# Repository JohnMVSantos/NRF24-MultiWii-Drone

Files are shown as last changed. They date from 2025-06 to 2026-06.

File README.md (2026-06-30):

# NRF24-MultiWii-Drone

This repository contains both software and electrical components for building a drone using the NRF24L01 radio modules and Arduino.

# New PCBs from PCBWay

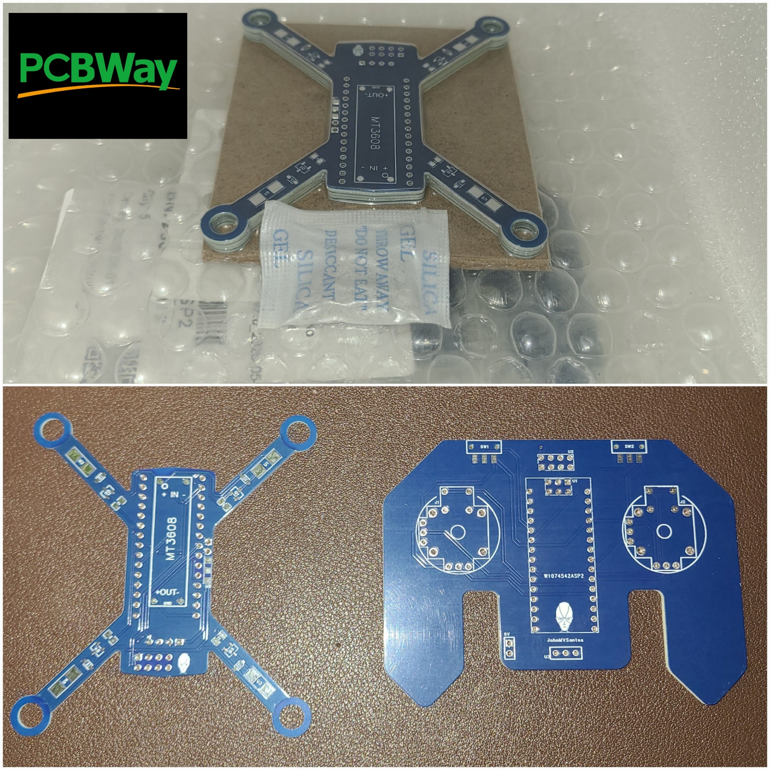
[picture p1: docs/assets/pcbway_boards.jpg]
PCBWay Boards


PCBWay provides an [excellent platform](https://www.pcbway.com/orderonline.aspx) for ordering and customizing your PCB designs. The platform provides easy-to-follow and easy-to-use PCB specifications that meets my needs such as setting the board quantity, the number of layers, the PCB thickness, material type, and much more! 

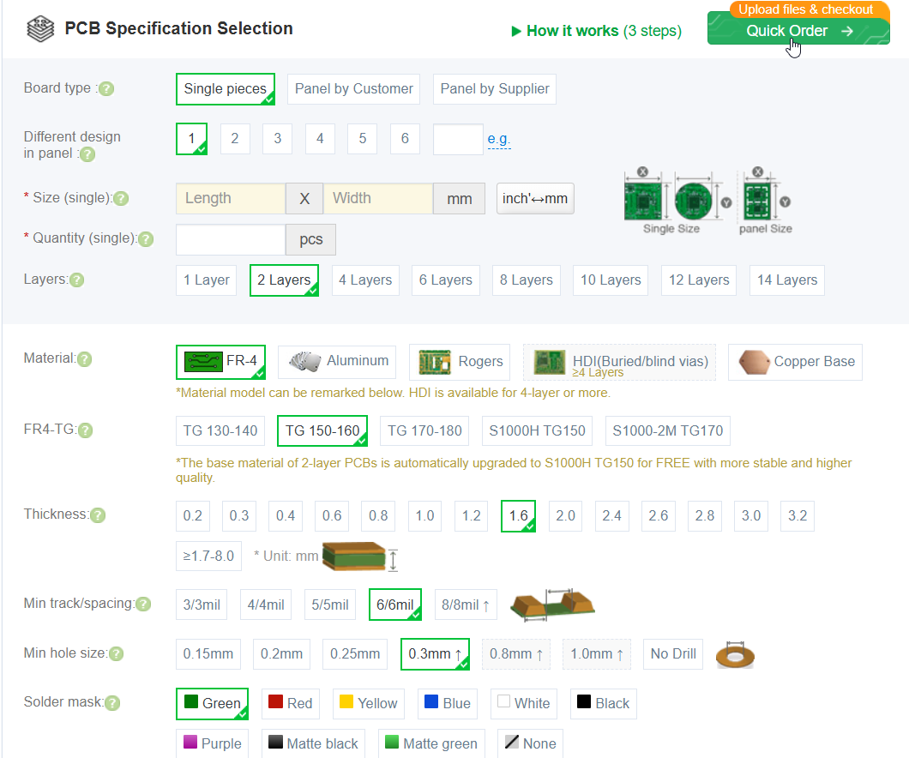
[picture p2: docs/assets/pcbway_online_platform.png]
PCBWay Online Platform


Furthermore, support is always available either through the platform or PCBWay will reach out to you directly if they require further specification or if they observe potential risks from their thorough review of your design.

Using PCBWay's online platform, I was able to import all my gerber files I designed using EasyEDA and successfully ordered the boards and arrived upon my location without any issues or concerns. This is a platform I would highly suggest for designers to use!

# Changelog

* Jun 08, 2025 [v1.0]: Prototype 1.0 [Fail] - Zero communication between controller and the drone.
* Jul 22, 2025 [v1.1]: Prototype 1.1 [Fail] - Drone short circuited with carbon fiber frame. 
* Aug 18, 2025 [v1.2]: Prototype 1.2 [Fail] - Drone keeps resetting.
* Aug 31, 2025 [v1.3]: [Prototype 1.3](https://youtu.be/l2KEjdwurtw?si=Yr7yQo37yw-8ZKtF) [Fail] - Drone does not lift off, motors out of sync. 
* Nov 30, 2025 [v1.4]: [Prototype 1.4](https://youtu.be/Q8TK0ZtKbdI?si=oR4hcLkOsZyx9zIT) [Fail] - Drone does not lift, too heavy, joystick movements does not match MultiWii simulation and drone output behaviour.
* Jan 31, 2026 [v1.5]: [Prototype 1.5](https://youtu.be/-AvNgkW_3SQ?si=GbaD0aLfVKiBPiV2) [Fail] - Drone does not lift, keeps resetting, joystick movements does not match flight pattern
* Mar 28, 2026 [v2.0]: [Prototype 2.0](https://youtu.be/SzuUDoo7Tts) [Fail] - Converted drone to a PCB, but still does not lift, one motor draws most of the power. Power to the components is not well regulated.
* Apr 27, 2026 [v2.1]: [Prototype 2.1](https://youtu.be/SVGbemywxcY) [Pass] - PCB adjustments to reduce EMF effects and better weight distributions; software adjustments for correct motor mapping.

[EasyEDA Project](https://oshwlab.com/john.santos/multiwii-arduino-drone-project)

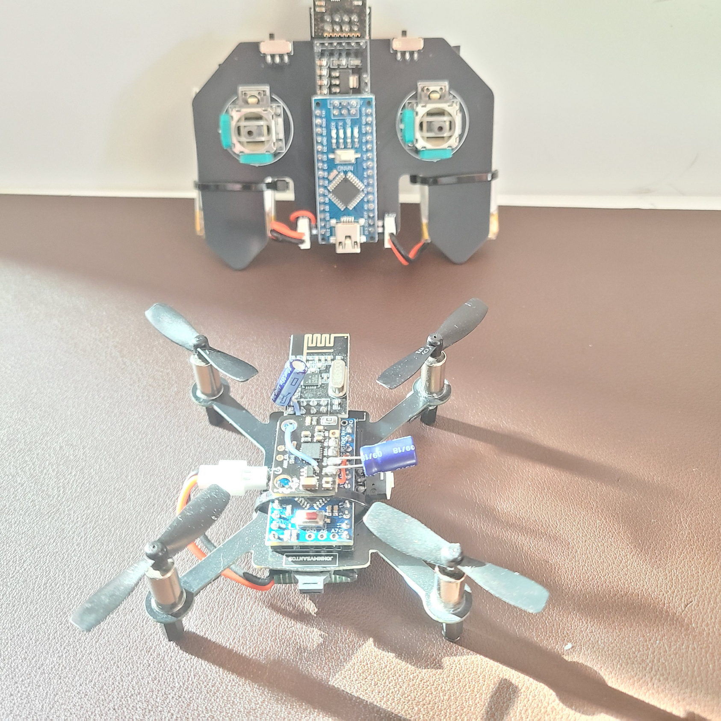
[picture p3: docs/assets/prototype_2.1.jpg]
Prototype Two


# Schematics and Diagrams

The following schematic diagram shows the wiring components and hardware for the drone.

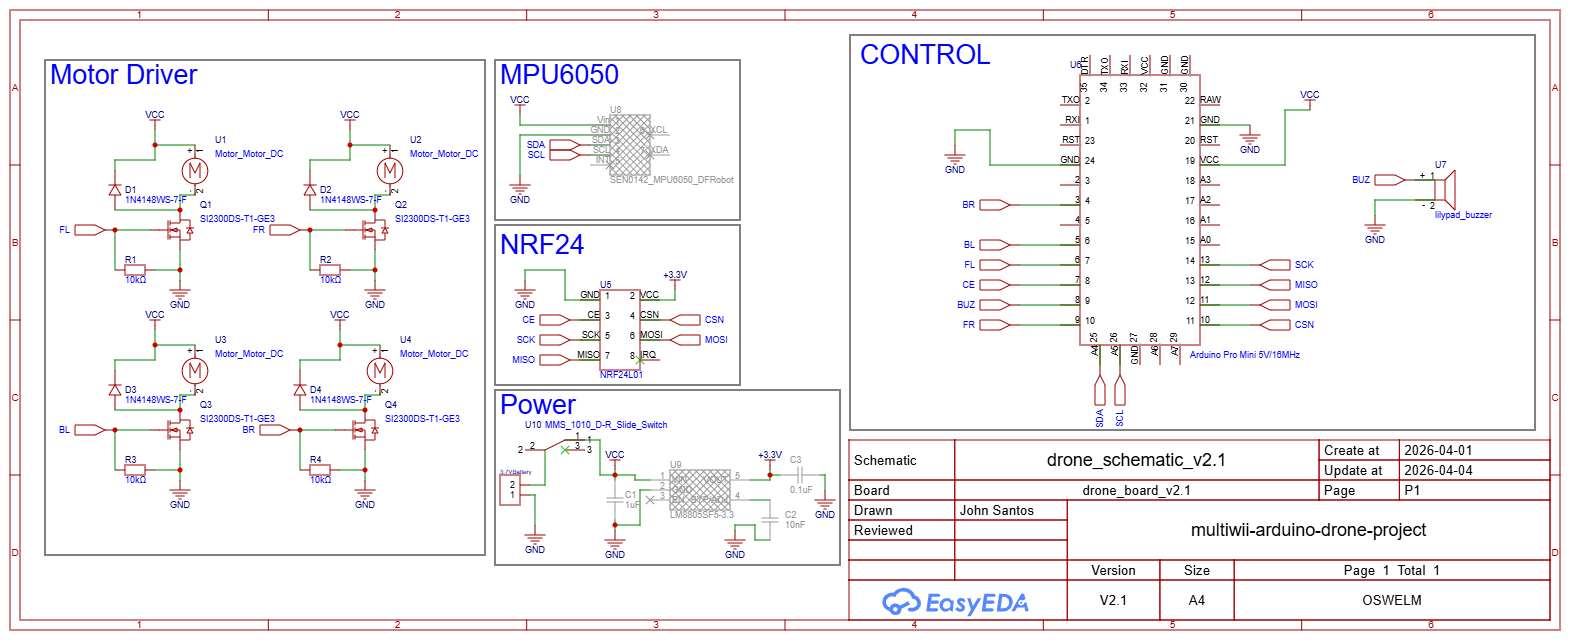
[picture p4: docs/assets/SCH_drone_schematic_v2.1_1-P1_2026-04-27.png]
Drone Schematic


| Drone PCB | Drone 3D View |
|---|---|
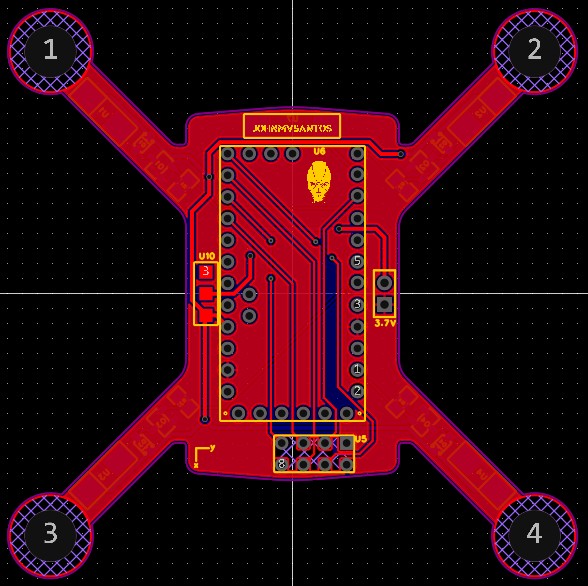
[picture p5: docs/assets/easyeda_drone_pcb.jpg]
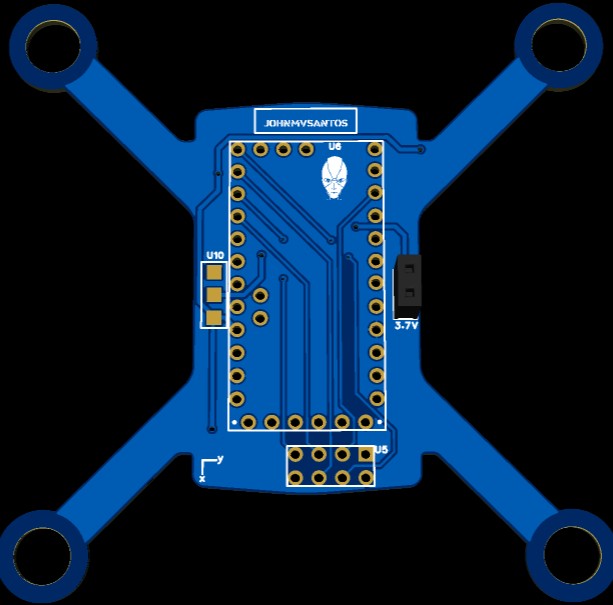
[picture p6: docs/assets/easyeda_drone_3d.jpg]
|  |  |

The following schematic diagram shows the wiring components and hardware for the drone controller. 

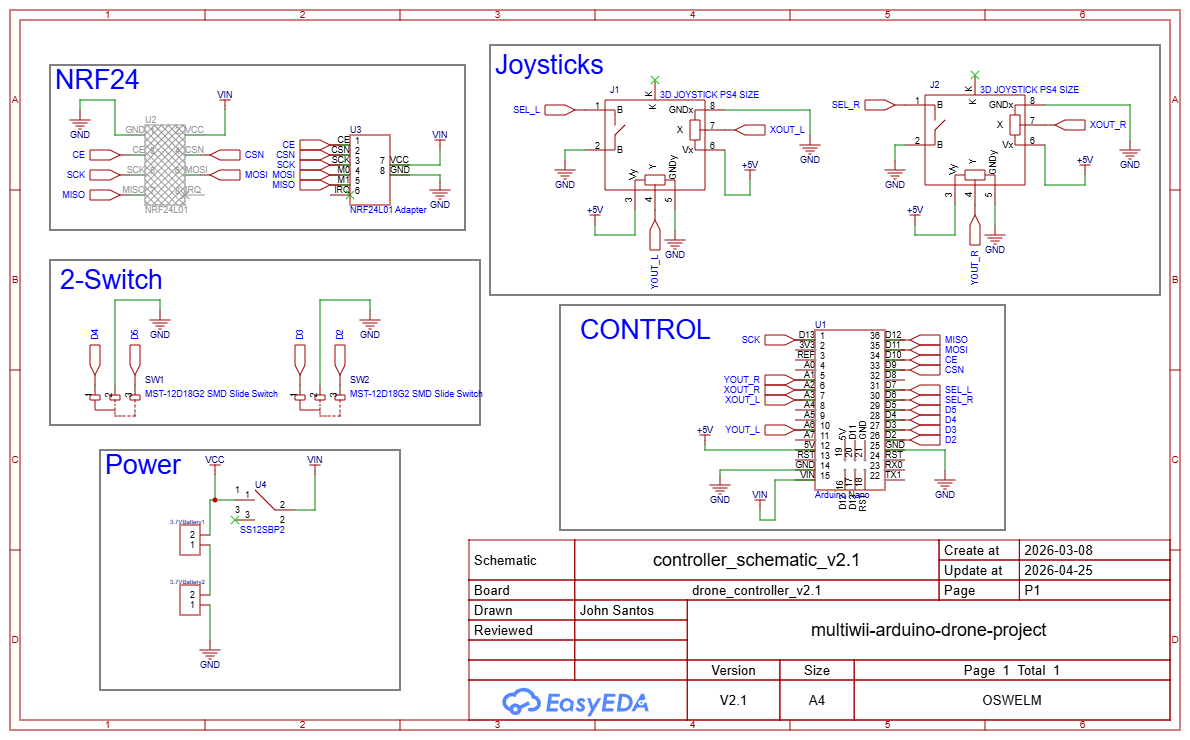
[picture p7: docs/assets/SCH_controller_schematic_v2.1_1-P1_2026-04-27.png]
Controller Schematic


| Controller PCB | Controller 3D View |
|---|---|
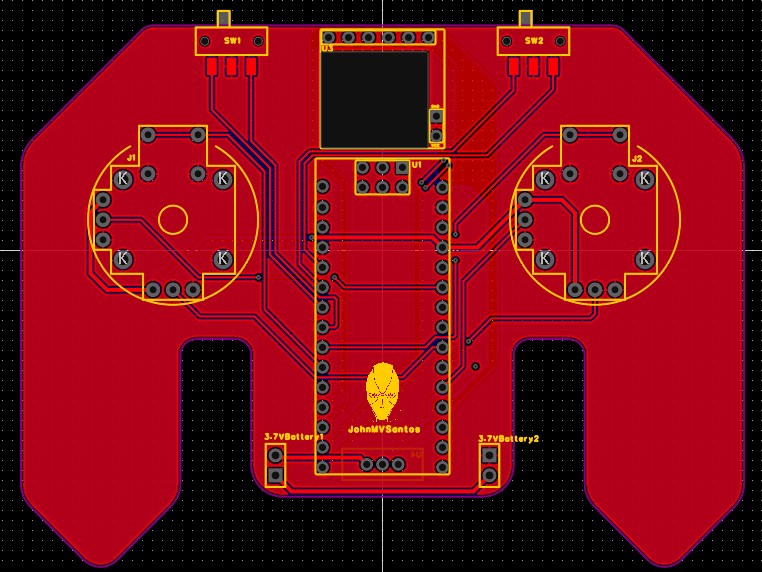
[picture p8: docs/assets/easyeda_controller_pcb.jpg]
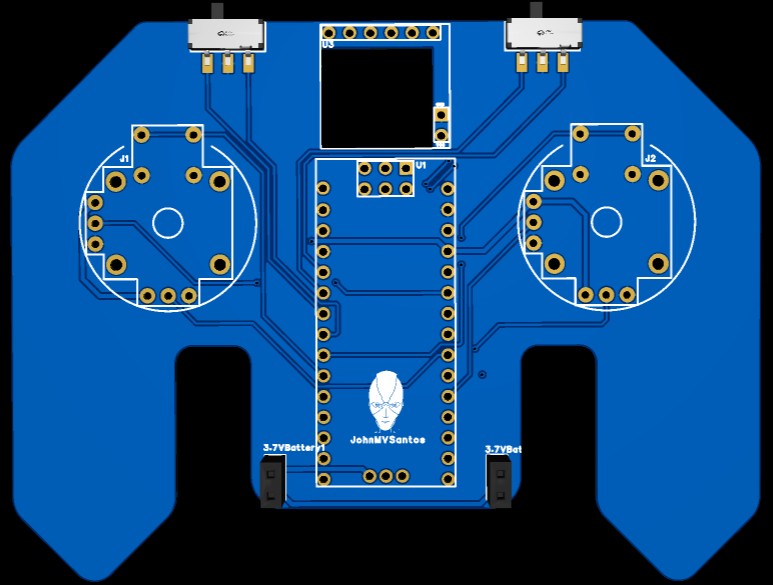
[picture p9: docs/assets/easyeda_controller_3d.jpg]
|  |  |

The following DXF sketch cutout of the drone can be found under `design_files/drone_sketch.dxf`.

| Drone Frame Sketch | Drone Frame Body |
|---|---|
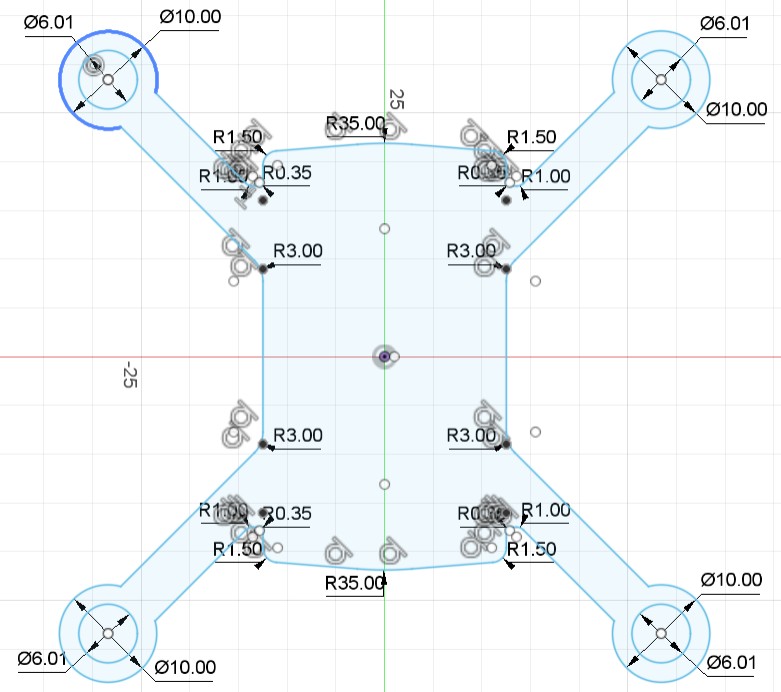
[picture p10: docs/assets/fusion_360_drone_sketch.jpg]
Drone Frame Sketch
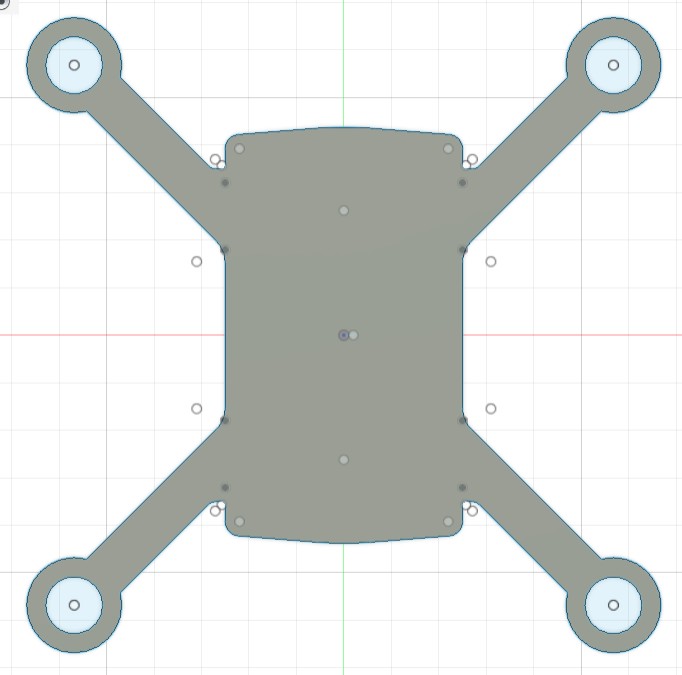
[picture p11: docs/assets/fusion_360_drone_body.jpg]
Drone Frame Body
|  |  |

The following DXF sketch cutout of the controller can be found under `design_files/controller_sketch.dxf`.

| Controller Frame Sketch | Controller Frame Body |
|---|---|
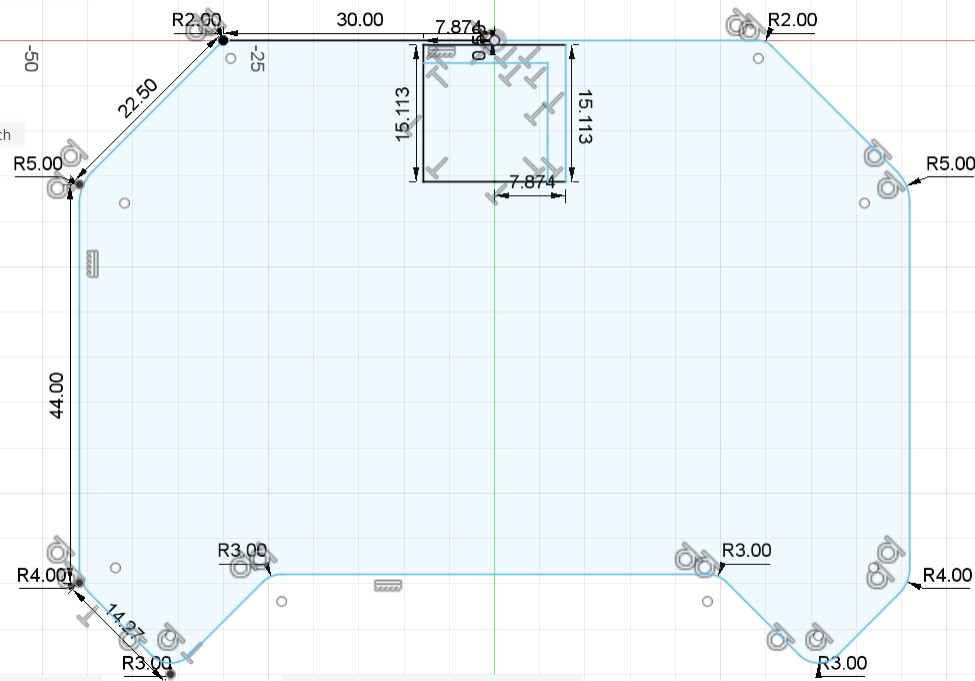
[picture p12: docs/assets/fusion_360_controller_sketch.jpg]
Controller Frame Sketch
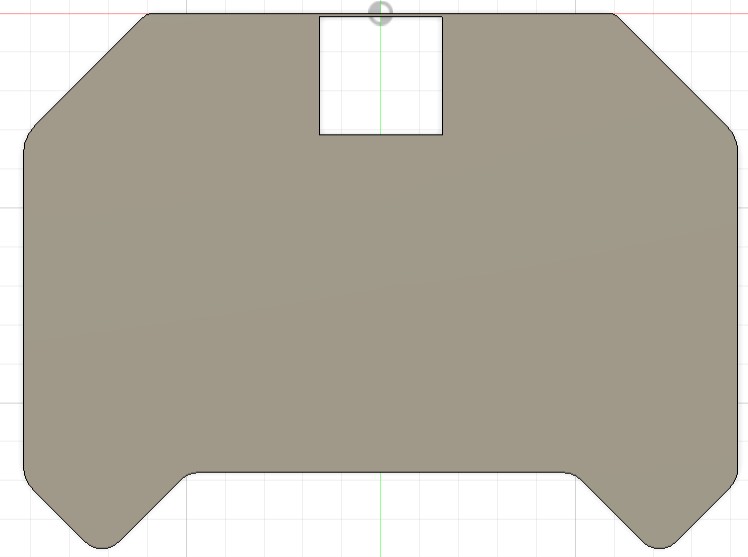
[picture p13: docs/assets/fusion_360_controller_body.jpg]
Controller Frame Body
|  | 

The tutorial for building and assembling the drone can be found under `\docs`.

# Documentation

The documentation that provides more details and tutorials on building the drone can be found under `\docs`. 

To generate the documentation using `sphinx`, follow the tutorial below with the command line. 

```shell
cd docs
```

```shell
pip install -r requirements.txt
```

```shell
make clean
make html
```

```shell
sudo apt-get install latexmk
sudo apt-get install texlive-fonts-recommended
sudo apt-get install texlive-latex-extra
```

```shell
make latexpdf
```

# Key Learnings/Takeaways

## Design Considerations:

1. Battery 25C works for this drone
2. 5V 16MHz Arduino Pro Mini is sufficient for the drone
3. Copper EMF blocking shield helps reduce the EMF noise generated by the motor driver
4. Better to place MPU6050 away from electrical noise of the Arduino and other electrical components
5. The IMU needs to be sitting flat and secured properly to prevent wobbling
6. Capacitors helps reduce power fluctuations and noise
7. Position all 4 motors evenly and in the same manner. The start rotation should be consistent
8. Smaller surface area can cause instability? I think it is better for longer arms and larger propellers to increase the drone surface area - larger lift
9. Thicker drone arms that doesn't bend is better for stability. The overall surface area of the arms and propeller should be maximized
10. Choose your components based on the design specifications. These are the components I have chosen based on the design specifications
    - 10KOhm resistor 0805 (0.125W) [CRG0805F10K](https://www.digikey.ca/en/products/detail/te-connectivity-passive-product/CRG0805F10K/2380831)
        * Ensures VGS = 0
    - Diode: [SS54FSH](https://www.digikey.ca/en/products/detail/taiwan-semiconductor-corporation/SS54FSH/18718584) (5A, 40V)
        * Maximum rated current must be greater than 2 * stall current (assuming 2-6A)
    - N- Channel Mosfet: [AO3400A](https://www.digikey.ca/en/products/detail/alpha-omega-semiconductor-inc/AO3400A/1855772) or [AO3416](https://www.digikey.ca/en/products/detail/alpha-omega-semiconductor-inc/AO3416/1855783)
        * VDS ~>20-30V is better (rated for high voltage spikes)
        * RDS ~<10mOhm is better (low power loss)
        * Gate threshold ~2.5-3.3V (turns on based on battery capacity)
        * Continuous & Pulsed Current Rating should exceed peak and continuous current draw in drone (5.5A = 25C * 0.22Ah).

1. Use an oscilloscope to check the PWM signals from the motor gates to see if it is causing sync issues with the motors - ensure consistent PWM frequency across all four motors

2. Test n-channel mosfet Integrity and ensure drain voltage approaches zero as gate voltage increases

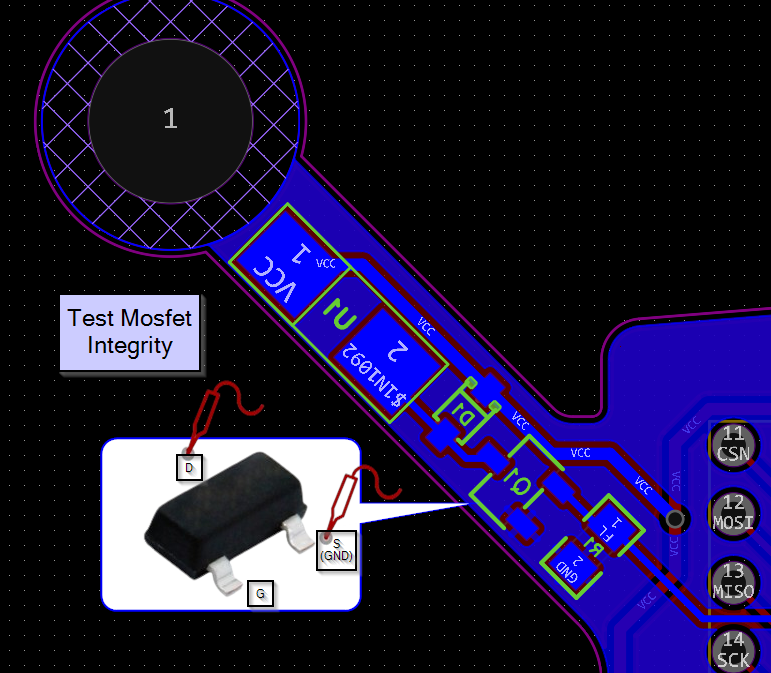
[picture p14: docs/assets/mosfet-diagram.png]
Mosfet Testing


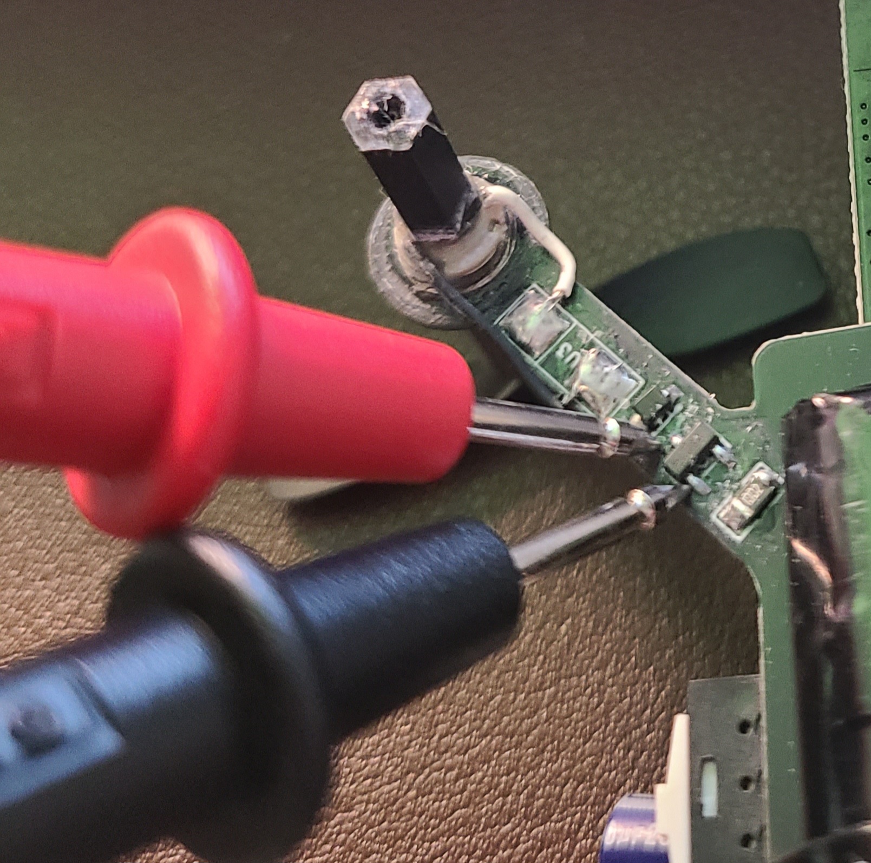
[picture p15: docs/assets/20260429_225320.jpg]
Mosfet Testing Probes


3. Test Motor terminals if voltage is received

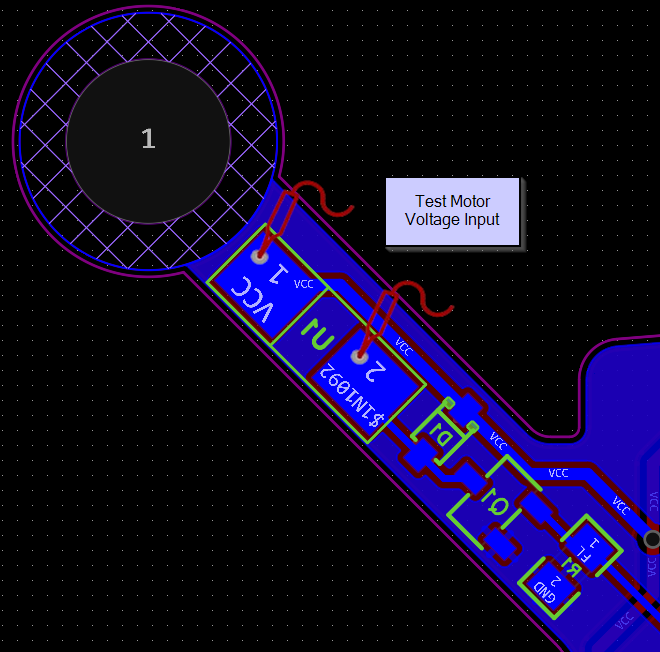
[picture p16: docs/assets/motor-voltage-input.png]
Motor Terminal Voltage


## Practical Considerations

1. Check NRF24 radio communication first before assembling the drone. Always test parts individually
2. Keep it simple and complexity should not come first. Achieve minimum functionality for initial developments
3. Better to use solder with lead, but prone to contamination (ensure proper storage)
4. Thin kapton tapes do not provide as much insulation as actual electrical tape. Though electrical tape is heavier
5. Ensure the motor power can carry the total load of the drone
6. Ensure prototype works before designing a final PCB

# Successful Vendors

These are the lift of successful vendors that sold the components needed for this project that worked. 

- **Robojax**: Arduino Pro Mini 5V 16MHz 
- **HiLetGo**: NRF24L01+PA+LNA Transeiver Module
- **Aideepen**: NRF24L01 Transeiver Standard Module
- **Aideepen**: Arduino Nano Board
- **Fytoo**: 3.7V 600mAH LiON batteries - used for the controller
- **Fytoo**: 3.7V 220mAH LiON 25C battery
- **WWZMDiB**: Mini USB to TTL Serial Converter Adapter, 3.3V/5.5 V FTDI Breakout Board for Arduino
- **Wishiot**: Thumb Joystick Module Dual Axis Sensor for Arduino
- **DFRobot**: MPU6050 Gyro + Accelerometer Module
- **Digikey**: Surface mount components (resistors, diodes, n-channel MOSFETs, capacitors, etc)
- **Midzooparts**: Lilypad Buzzer Small Speaker Module for Arduino
- **Crazepony**: 4pcs 6x15mm Motor (Speed: Insane) 19000KV, 70000 RPM@3.7V

These are the list of vendors that sold components that did not work or were faulty for this project.

- **Hutomwua**: Arduino Pro Mini 5V 16MHz (Did not meet specifications or seems to be 10MHz on the backside - not advertised)
- **ELEGOO**: Arduno Nano (Faulty and did not program)
- **Fytoo**: 3.7V 1000mAH LiON batteries (potentially drew too much current and burned the board?)
- **Aideepen**: NRF24L01+PA+LNA Transeiver Module (Faulty and did not communicate)

# Future Work

## v3.0
- If it doesn't fly (use Arduino Nano board and standard MPU6050? This requires regulators since Arduino Nano inputs 5V)
- Incorporatte FPV camera - make it see
- Add AI detections and features

## v4.0
- Custom FPV GUI with IMU readings (Can a single transmitter have two recievers (Controller + GUI)? )

# Credits

Original drone software is credited to [iforce2d](https://www.youtube.com/@iforce2d).

## Drone Tutorial - Max Imagination

Watch the video (https://www.youtube.com/watch?v=Sa6EslOHsI0)

* [Elektor Labs blog post](https://www.elektormagazine.com/labs/make-a-tiny-arduino-drone-with-fpv-camera)
* [Project Files](https://drive.google.com/drive/folders/1mWTCPN2daOcmTa4wUF0j8qPXhXvxLfkK)

## Drone Tutorial - ElectroNoobs

Watch the video (https://www.youtube.com/watch?v=J0x4ChjUS00&t=719s)

# Support Forums

* https://www.instructables.com/Make-a-Tiny-Arduino-Drone-With-FPV-Camera/
* https://www.elektormagazine.com/labs/make-a-tiny-arduino-drone-with-fpv-camera

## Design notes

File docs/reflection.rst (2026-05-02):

.. _reflection:

Reflection
===========

Log Entry: June 8, 2025
------------------------

The inspiration behind this project stems from `Max Imaginations' Mini FPV Drone Tutorial <https://www.youtube.com/watch?v=Sa6EslOHsI0>`_. 
Watching that video sparked the idea to create a similar design with my own custom modifications to better understand the process of engineering design.
Having recently graduated with a bachelor's degree in electrical engineering, I wanted to build more experiences in the field of electrical engineering. 
I found that by embarking on this project, I could apply my knowledge I gained in my studies to a practical application and also explore new concepts and ideas along the way.

It was not easy to commit to the project in the beginning because deep down I knew that I would be spending a lot of time and resources on this project even more so that this project
requires a lot of electrical and mechanical components that could be quite expensive. Furthermore, I am also working full-time as a software engineer and finding 
free time to work on this project was a challenge. Alot of the time spent on this project was during the weekends and late nights after work which required a lot of sacrifice. 

However, I was determined to see this project through; to better myself as an electrical engineer and to create something new and challenging despite my lack of 
personal experiences in building drones or electrical engineering projects in general. 

The start of the project was slow as I had to first list all the electrical and mechanical components I needed to build the drone and its controller. I wanted to 
gather as much detail as possible such as the cost, size, and weight of each component to assess its viability. Most of the components I had used 
remains the same as Max Imaginations' Drone, but I wanted my own custom design of the frame.

After listing the components for the drone and the controller, I had started to replicate the wooden frame design by Max Imagination, but after recreating the frame,
I found that it was too small and simple looking for my liking. I wanted a more streamlined and modern design so I explored other designs online that uses carbon fiber. 
I eventually sketched out a design that I liked and drew a blueprint of the components for my frame as a cutout template. I then moved on to purchasing a 0.5mm thick carbon fiber sheet.
I printed the cutout template and made the cutouts on the carbon fiber sheet for each component of the frame using a dremel tool. The frame was eventually built
using carbon fiber and M2 screws and nuts to hold the components in place.

The next step was building the electrical components of the drone. I had to first study the circuit provided by Max Imaginations' Drone and I also redrew the circuit in EasyEDA for my own references.
After drawing the circuit schematics for the drone and the controller, I then purchased the components from Amazon, Digikey, and Mouser. This stage was also a bit slow as I had to 
wait for the components to arrive before I could continue with the project. There were a lot of delays due to some parcels being lost and I had to reorder these lost components from different sources. 

Once all the electrical components arrived, I started building the circuit for the drone by soldering the components together. I had little experiences with soldering
electrical components so I had some challenges in this area. Primarily, the soldering iron oxidized quickly which is probably due to poor techniques I am employing or poor
solder material that I am using. I had to switch solder tips quite frequently, but this wasn't very efficient as I ran out of solder tips and I was forced
to use an ineffective soldering iron which led to poor soldering quality. This stage started to take a bad turn for me as the poor soldering quality 
affected the overall quality of the design as the circuit was prone to short-circuiting and the components not working as expected.

I reached a stage where I had the circuit for the drone built and assembled and programmed using Arduino, but there were lots of failures in MultiSim. The drone was able to 
be programmed, but it did not interface well with MultiSim as the MPU6050 Gyro movements was not translated in the simulation and only appeared as a bunch of noisy signals. Furthermore,
the MPU only seemed to move digitally when grounding pin D12 on the Arduino Pro Mini which was not expected. At this stage I was not satisfied with the current work on my drone as I am starting to
see failures and weaknesses in my design. So I had to take a step back and reflect on my design and make revisions to resolve the issues I was facing. I've documented
the issues with this design which I have indicated as "Prototype 1" under the :ref:`Prototypes section <prototypes>`.

In this stage, I have planned to recreate the design and name it as "Prototype 1.1" with the fixes needed for the issues from the current design.

Log Entry: July 22, 2025
-------------------------

This log will provide details to the outcome of Prototype 1.1 and the revisions made to the design. This prototype had a much more compact design 
with shorter connections and lighter wires. Furthermore, the controller had a proper enclosure recycled from a toy controller enclosure with modifications
to fit the new components. However, this prototype also failed the final testing. The initial work for this prototype started by assembling the electrical components by resoldering the drone circuit using 28 AWG silicon copper wires. 
After the drone circuit is complete, the next task was to modify an old toy controller enclosure to fit the new controller components. This task involved drilling and cutting
certain parts of the enclosure using a dremel tool. Once the enclosure was fitted, the new components were installed and soldered. 

In this stage, the drone circuit and the controller circuit are both assembled and programmed for testing. The first test on the drone had some success
in which the IMU was able to ready the gyro movements. However, the flight controls in MultiSim were still unresponsive to the joystick movements from the controller. I found later
on that the radio modules from the controller were faulty. This test involved setting up a simple communication between two of the spare radio modules
on a breadboard. After reordering a new set of radio modules, I was able to get clear communication between these new modules. Moving forward, the drone
was also able to capture the signals sent from the controller's joystick movements as shown in MultiSim. Lastly, I was not fully confident that the drone enclosure was properly insulated,
so I tested the drone responding without it's enclosure. This testing was successful as the motors properly relayed the controller's signals with the expected
motor speed based on the throttle joystick movements. However, the drone failed once I tested with the drone enclosure attached. I suspect, I had short circuited the electrical components of the drone
because of its carbon fiber frame. I had regretted not testing the insulation of the frame even with Kapton tape. Again at this point, I needed to take a step back again
and assess the failures of this prototype and make more revisions to resolve these issues. More details of this assessment are provided under the :ref:`Prototypes section <prototypes>`.

In this stage I have ordered replacements for the damaged components such as the Arduino Nano, Arduino Pro Mini, NRF24L01 radio modules, and the controller battery.
I have planned to recreate the design and name it as "Prototype 1.2" with the fixes needed for the issues in the current design.

Log Entry: August 18, 2025
---------------------------

This log will provide details to the outcome of Prototype 1.2 and the revisions needed to be made for the design. After implementing this prototype, the behaviour of the drone
was quite erratic. The drone kept resetting when throttle is decreased near zero. It seems to keep resetting and attempts to recalibrate the IMU. The motor responses were rare and seldom spins. When the motor does respond, it 
responds in bursts and then the drone resets. Looking at the MultiSim outputs, the AUX1 and AUX2 were correctly translated including the joystick movements for roll, pitch, yaw, and throttle levels. So I don't think the issue
has to do with the controller, rather with the drone itself. 

I suspect possible issues with the drone circuit listed below.

1. The battery discharge rate is too low (25C) and that a proper drone battery with a higher discharge rate (30C or higher) is needed
2. The power for the radio is not consistent and requires a 10uF filtering capacitor at the NRF24 power inputs
3. The power for the Arduino Pro Mini is not consistent and requires a 100uF filtering capacitor
4. The power lines has a large AWG (small thickness) where the current cannot be supplied properly
5. Motor PWM signals could be too weak to drive the motors
6. Potential EMF noise or leaks is affecting the IMU readings? 
7. The Arduino Pro Mini is faulty which was purchased from "Hutomwua". The previous prototypes was working which was purchased from "Robojax"

Looking for a battery replacement greater than 25C was quite a challenge as most of the batteries I found were 25C or lower. It was recommended to use "Turnigy Nano-Tech" batteries for their high performance,
but these were always not available and kept being out of stock due to their high demand. Although I did manage to find a 30C LiPO battery, not from Turnigy, but from AMZZN, it still didn't
resolve the main issue. The drone behaved a bit better, but most of the resetting issue persisted. 

I moved forward by adding filtering capacitors at the radio module and Arduino Pro Mini power inputs, but this did not resolve the issue. I also ensured the solder for the power connections and the 
radio connections were solid and well connected, but this also did not resolve the issue. I even created a new motor driver with new MOSFETs and diodes as I had assumed this circuit also short circuited from the previous prototype, but this still this replacement did not resolve the issue. 

I then suspected, it has to do with the software and that the PWM signals were too weak to drive the motors. Unfortunately, I do not have an oscilloscope to verify the weake PWM signals, but I found the factor in the MultiWii software
that tunes the PWM outputs. Following the tutorial by Max Imaginations, the variable should be `float adjustmentFactor = 0.255` in line 1069 of output.cpp. I set this value to 0.255 from the default of 1, but this did not resolve the issue. However, it did tune the buzzer noises lower.
As a future work, it seems that it will be best to purchase an oscilloscope to confirm this suspicion. 

Moving forward, I retraced my steps and assessed the instructions for properly arming the drone using MultiSim. First the AUX1 and AUX2 should be set high for arming the drone and the beeper respectively. Once set, the drone accelerometer should
be calibrated and then read and write to save the changes. To arm and calibrate the drone, the AUX1 should be set low and the throttle and pitch controls are set to zero until the calibration noises are in effect. Once in effect, wait atleast 3 seconds
to apply the calibrations. With these steps, the drone still didn't manage to respond. 

My next suspicion is the hardware itself. I purchased the Arduino Pro Mini from "Hutomwua" which did not work, I intend to purchase the Arduino Pro Mini from "Robojax" which worked in the previous prototype (v1.1) where the motors actually responded. 
I have purchased the same Arduino Pro Mini and will try again in the next version. Furthermore, I will confirm the specifications for the MOSFETs, diodes, and resistors are properly rated for the circuit and the power requirements. More details of this assessment under the :ref:`Prototypes section <prototypes>`.
I have planned to recreate the design and name it as “Prototype 1.3” with the fixes needed for the current design.

Log Entry: August 31, 2025
---------------------------

This log will describe the details to the outcome of Prototype 1.3 and the revisions made to the design. Based on the last suspicion that the hardware purchase for the Arduino Pro Mini
was the source of the issue. This suspicion turned out to be true. Looking at the Arduino Pro Mini purchased from "Hutomwua", the board frequency was only 10MHz (from the backside). This did not meet specifications 
for a 5V 16MHz board. I repurchased the Arduino Pro Mini from "Robojax" which was 5V 16MHz and this resolved the issue. The drone was able to respond to the controller's joystick movements.

However, the design is still not perfect as further issues continued. Although the motors responds to the joystick movements, the drone behaves erratically unable to make a proper liftoff.

The possible issues are listed below.

1. The drone is not calibrated properly
    - The drone needs to sit on a flat surface for a proper calibration
    - The accelerometer and the gyroscope needs proper calibration
    - Adjust settings in MultiWii configuration with max smoothness
2. Motor direction is wrong
    - This can be verified by feeling if the air is being pushed upwards
    - Record slow motion video to see the direction of the motors
3. The motor RPMs are not the same and unsynchronized
4. The forward direction of the MPU6050 is in the opposite direction
    - Rewire orientation of the motors to have face the MPU6050 in its forward direction
5. The drone is still too heavy and certain weights of the components are not balanced causing the center of gravity to be offset
    - Remove heavy motor mounts and just rely on superglue to attach the motors
6. The arms of the drone are limble which causes wobbling during flight
    - Reinforce the arms with a stronger material that doesn't bend such as popsicle sticks

More details of this assessment under the :ref:`Prototypes section <prototypes>`. I have planned to recreate the design and name it as “Prototype 1.4” with the fixes needed for the current design.

Log Entry: November 30, 2025
-----------------------------

This log will describe the details to the outcome of Prototype 1.4 and the revisions made to the design. In this prototype, the drone accelerometer was calibrated 
and an EMF copper blocking shield was installed to prevent interference from the motor controller to the Arduino Pro Mini. Furthermore, the motor direction was verified
where the top left motor spins clockwise, top right motor spins counter-clockwise, bottom left motor spins counter-clockwise, and the bottom right motor spins clockwise. 
The bottom right propeller was wrong preventing the air from being pushed downward. Furthermore for stability reasons, the arms were replaced with popsicle sticks
to prevent any bending or oscillations, the motors were also superglued to the arms. 

Although the design is still not perfect as further issues continued. The possible issues are listed below.

1. IMU wobbles, unsecure mount
2. Frame is yet still too heavy
3. Smaller propellers + arm surface area - more unstable
4. Battery is mounted at the bottom which makes it hard to connect
5. Wrong drone output behaviour from the joystick movements - needs software correction
6. Needs PID tuning for the roll, pitch, and yaw

New Frame Requires:
- Lighter, thinner frame
- Thick arms with more propeller surface area
- Battery mounted on top for easier connection and center of gravity adjustment
- Superglued motors and soldered connections
- Reduce weight as much as possible

The current configurations with the expected behaviour and the actual behaviour are noted below

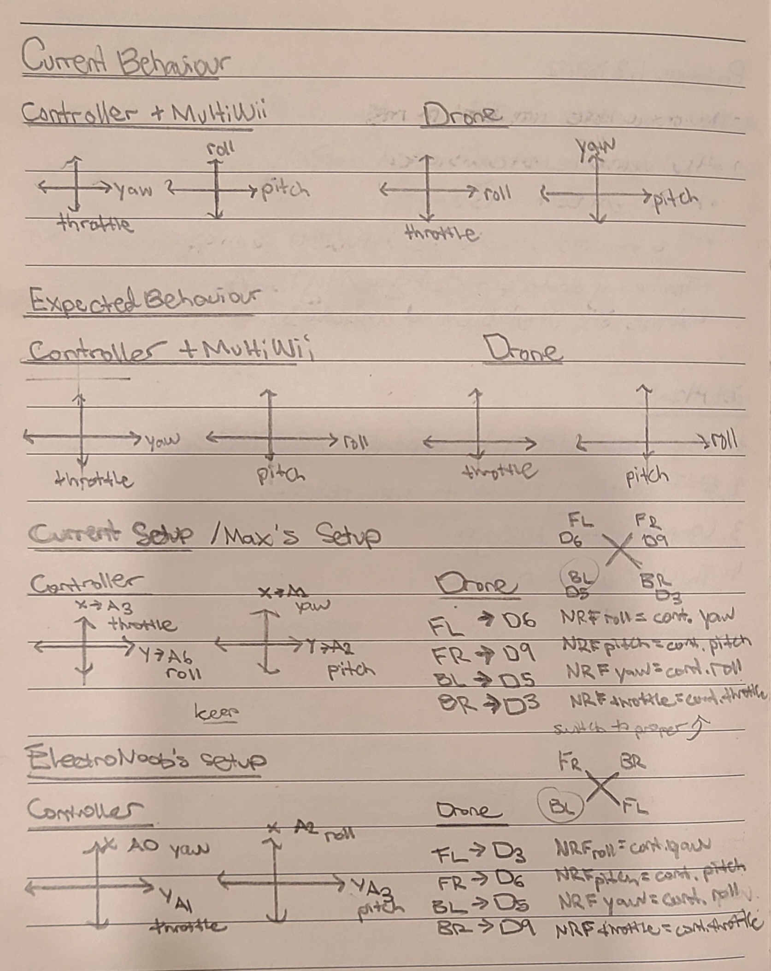
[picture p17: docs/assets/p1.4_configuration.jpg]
Prototype 1.4 Configuration


More details of this assessment under the :ref:`Prototypes section <prototypes>`. I have planned to recreate the design and name it as “Prototype 1.5” with the fixes needed for the current design.

Log Entry: January 31, 2026
----------------------------

This log will describe the details to the outcome of Prototype 1.5 and the revisions made to the design. 
This prototype is based on redesigning the frame to use popsicle sticks and superglue to reduce the overall weight of the drone and to secure the components in place.
However, this prototype is still unable to lift off, and suspecting it could be due to weight imbalance of the components, the motors spin at different RPMs and unsynchronized, or the motors spin in the wrong direction as I felt the air being pushed upwards with my hand. 

The next prototype will explore designing a custom PCB for the drone to reduce the wiring connections and to have a more compact design. Furthermore, I will also explore different motor driver components to withstand potential current or 
power rating issues. More details of this assessment under the :ref:`Prototypes section <prototypes>`. I have planned to recreate the design and name it as “Prototype 2.0” with the fixes needed for the current design.

The possible reasons for the resetting issue are listed below.
1. The Arduino Pro Mini is not receiving enought power (needs 5V, but getting only 3.3-4V)
2. Power should be directly to raw pin instead of VCC pin, or both?
3. Update MultiWii settings exactly to Max Imagination's settings
4. Resistor at the reset pin to avoid constant drone resetting? (Resetting is primarily due to EMF effects or loss of power from the battery)
5. Missing EMF blocking copper sheet under the IMU (cover with clear tape and add ground wire)
6. EMF Copper Blocking Shield under the Arduino Pro Mini- [Helped with wobbling]
7. Software issue? Try disabling FORCE_GYRO settings in the software

Experimented with possible solutions to out of sync motors.
1. Issue with propeller - Wrong propeller used on back left [Helped with stability]
2. Motor direction is correct (top left is CW, top right is CCW, bottom left is CCW, bottom right is CW)
3. Solder motor wirings directly - [Helped with loss of power to the motors]
4. Switch forward/backward motor wirings + Max's MultiWii settings. [Was not quite useful]
5. Research imbalance, seems that left side of the drone pulls up more:

	- incorrect flight controller orientation
	- wrong motor/propeller configuration
	- or a damaged component like a motor or ESC

A list of unknowns I encountered.
1. On multiwii the IMU yaw just rotates even though the drone is placed flat on the table.
2. Calibrate controller settings to match joystick?
3. Max Imagination's right joystick is rotated - should also rotate

Log Entry: March 28, 2026
----------------------------

This log will describe the details to the outcome of Prototype 2.0 and the revisions made to the design. In this prototype, a PCB was designed in EasyEDA and manufactured in JLCPCB.
The motivations behind this design is to stablize the wiring connections and to have a more compact design.  Furthermore, I have also chosen chosen different motor driver components
to withstand potential current or power rating issues. These are the final components I have chosen for this prototype.

- 10KOhm resistor 0805 (0.125W) [CRG0805F10K](https://www.digikey.ca/en/products/detail/te-connectivity-passive-product/CRG0805F10K/2380831)
        * Ensures VGS = 0
- Diode: [SS54FSH](https://www.digikey.ca/en/products/detail/taiwan-semiconductor-corporation/SS54FSH/18718584) (5A, 40V)
    * Maximum rated current must be greater than 2 * stall current (assuming 2-6A)
- N- Channel Mosfet: [AO3400A](https://www.digikey.ca/en/products/detail/alpha-omega-semiconductor-inc/AO3400A/1855772) or [AO3416](https://www.digikey.ca/en/products/detail/alpha-omega-semiconductor-inc/AO3416/1855783)
    * VDS ~>20-30V is better (rated for high voltage spikes)
    * RDS ~<10mOhm is better (low power loss)
    * Gate threshold ~2.5-3.3V (turns on based on battery capacity)
    * Continuous & Pulsed Current Rating should exceed peak and continuous current draw in drone (5.5A = 25C * 0.22Ah)

However, despite the changes to the design, this drone is still unable to fly and behaves more poorly. When testing the assembled PCB, it looks like most of the current
is being drawn towards the back right motor causing it the only motor to spin. When I disconnect this motor, the other three motors spin, but the resetting issue persists. 
It looks like separating the motor driver across the arms does not mitigate the EMF effects causing the drone to keep resetting. I also tried adding a 100uF capacitor between the power
and ground pin of the MPU6050, but this does not resolve the reset issue. 

These are the list of issues for this prototype.

- Bottom right motor keeps spinning uncontrollably and the only single motor that spins when all motors are connected (need to find a way to separate power between the motors and the microcontroller)
- Better larger battery did not help
- 100uF at the MPU6050 did not help
- Thicker power lines by reinforcing the connections with external wires did not help 
- Drone still keeps resetting
- MultiWii is an old software and no longer used - may not even be properly installed due to requiring a specific Java version. 

The possible reasons for these issues are listed below.

1. Power management issues - the battery is not strong enough to drive both the Arduino Pro Mini and the Motors
2. Power lines are too thin
3. All lines in this PCB are set to 0.254mm which is the default in EasyEDA. Also the power lengths to the motors should be similar
4. 90 degree line traces are evident in these connections which can cause impedence issues

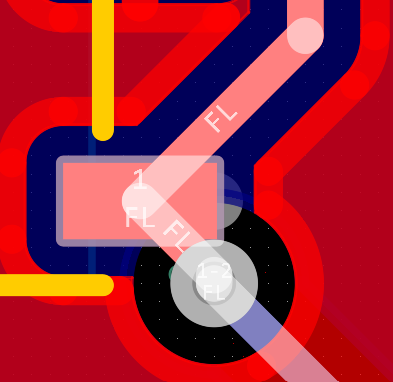
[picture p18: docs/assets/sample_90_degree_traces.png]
90 Degree Line Traces


5. Absence of grounded EMF copper blocking shield - a bit hesitant with this since I have tried it before and it did not resolve the resetting issue
6. Props are placed wrong (air is pushed upward)
7. Motor placement are not consistent - wiring needs to be at the same start rotation
8. Use the exact same components as Max's design such as 1N4148
9. Need to use better power switch (SPST) - might not be driving enough current to the motors
10. Would adding filtering capacitors at the motors help?
11. Check PWM signals from motor gates see if it is causing sync issues with the motors
12. Test controller linear increase in throttle to see if all motors respond consistently
13. Test individual motors at full power with scale load?

Log Entry: April 26, 2026
---------------------------

This log will describe the details to the outcome of Prototype 2.1 and the revisions made to the design. 
The PCB design involves placing the motor driver at the bottom layer along the arms of the drone. 
This was an excellent design choice since the drone was more stable and the resetting issue was less frequent which could indicate the EMF effects towards the microcontroller was reduced. 
Furthermore, I have tried to balance the weight by distributing the components more evenly on the PCB. For example, the ON/OFF switch and the power pins are placed in opposite ends of the drone; the NRF24L01 is more centered and finally the battery is secured at the bottom centered on the PCB.
I have also used a better battery with a higher discharge rate of 30C, 450mAH, and 3.7V for better power supply to the drone. 
I have also updated the power lines to be 0.45-0.50mm thick in comparison to traditional lines only at 0.254mm thick. This reduces resistance added on the power lines for more direct current flow. There are also no 90 degree traces in the PCB design which can cause impedance issues. 
These power lines also have similar lengths to ensure the power is distributed evenly across the motors.
I have also reverted to using 1N4148 diodes and S12300DS n-Mosfets for the motor driver as these are commonly used in drone motor drivers and should be sufficient for the power requirements of the drone. Although I have noticed that one of the mosfets burned out and had to replace this - this occurence was uncommon.
It was necessary for me to add 10uF capacitors at the power inputs of the NRF24L01. Otherwise, the signal becomes lost and the drone throttle continuously increases until it reaches the maximum state; throttle down is no longer responding. This issue caused two of the motors (FL and BL) to burn out. After adding this capacitor, the signal is more stable and the drone responds properly to the controller's commands.
Though the front left motor is unstable - sometimes doesn't spin (no issues in the  mosfets or diodes in the driver) - poor motor/connection is plausible.
In addition, I have also added 100uF capacitor at the power input of the MPU6050 to stabilize any remaining reset issues. After adding this capacitor, I no longer found any occurences of the drone resetting.
The motor placements are also more consistent and the wiring is at the same start rotation. The propeller placements are also correct as the air is being pushed downwards.
Next I have checked the frequency of the PWM signals at full power to ensure it is consistent across all motors. Using an oscilloscope, I found that each PWM pins outputs a consistent 5.0MHz which is enough to drive the motors.
In the MultiWii software, I have simulated alot of movements in the drone to ensure the IMU correctly translates the drone movements.

The biggest change was remapping the motor designations in the software output.cpp based on the following comparisons to various projects and pin designations.

.. list-table:: Motor Pin Configuration Comparison
   :header-rows: 1
   :widths: 15 20 25 18 10 15

   * - Motor
     - Intended Orientation
     - Max Imagination (Current Setup)
     - Electronoobs
     - Code
     - Test Results
   * - Motor[0]
     - BR
     - D3
     - D9
     - D9
     - FR
   * - Motor[1]
     - FR
     - D9
     - D6
     - D6
     - FL
   * - Motor[2]
     - BL
     - D5
     - D5
     - D5
     - BL
   * - Motor[3]
     - FL
     - D6
     - D3
     - D3
     - BR

It seems that the code matches Electronoobs setup. Since I have followed Max Imaginations PWM wirings, I have to modify the software to reflect this wiring. 

Thus the software needs to match the following configuration.

* Motor[0] => FR
* Motor[1] => FL
* Motor[2] => BL
* Motor[3] => BR

So the following lines in output.cpp was modified to:

**Before**

.. code-block:: shell

    motor[0] = PIDMIX(-1,+1,-1); //REAR_R
    motor[1] = PIDMIX(-1,-1,+1); //FRONT_R
    motor[2] = PIDMIX(+1,+1,+1); //REAR_L
    motor[3] = PIDMIX(+1,-1,-1); //FRONT_L

**After**

.. code-block:: shell

    motor[0] = PIDMIX(-1,-1,+1); //FRONT_R
    motor[1] = PIDMIX(+1,-1,-1); //FRONT_L
    motor[2] = PIDMIX(+1,+1,+1); //REAR_L
    motor[3] = PIDMIX(-1,+1,-1); //REAR_R

Regarding the controller, I have also designed a PCB version of the controller. However, the inital protoype is still better at maintaing the communication with the drone. I still need to take a closer look into why the connection quickly gets lost with this new controller, despite the same connections.
I will try adding a filtering capacitor at the power input of the NRF24L01 to stabilize the signal and reduce noise. Otherwise, I will take a look at reusing the same NRF24L01 that works from the previous controller prototype.

Key Learnings/Takeaways
-----------------------

Design Considerations:

1. Battery should be 25C and higher
2. 5V 16MHz Arduino Pro Mini is sufficient for the drone
3. Copper EMF blocking shield helps reduce the EMF noise generated by the motor driver
4. Better to place MPU6050 away from electrical noise of the Arduino and other electrical components
5. The IMU needs to be sitting flat and secured properly to prevent wobbling
6. Capacitors helps reduce power fluctuations and noise
7. Position all 4 motors evenly and in the same manner. The start rotation should be consistent
8. Smaller surface area can cause instability? I think it is better for longer arms and larger propellers to increase the drone surface area -larger lift
9. Thicker drone arms that doesn't bend is better for stability. The overall surface area of the arms and propeller should be maximized
10. Choose your components based on the design specifications. These are the components I have chosen based on the design specifications

- 10KOhm resistor 0805 (0.125W)   `CRG0805F10K <https://www.digikey.ca/en/products/detail/te-connectivity-passive-product/CRG0805F10K/2380831>`_
    * Ensures VGS = 0
- Diode: `SS54FSH <https://www.digikey.ca/en/products/detail/taiwan-semiconductor-corporation/SS54FSH/18718584>`_ (5A, 40V)
    * Maximum rated current must be greater than 2 * stall current (assuming 2-6A)
- N- Channel Mosfet: `AO3400A <https://www.digikey.ca/en/products/detail/alpha-omega-semiconductor-inc/AO3400A/1855772>`_ or `AO3416 <https://www.digikey.ca/en/products/detail/alpha-omega-semiconductor-inc/AO3416/1855783>`_
    * VDS ~>20-30V is better (rated for high voltage spikes)
    * RDS ~<10mOhm is better (low power loss)
    * Gate threshold ~2.5-3.3V (turns on based on battery capacity)
    * Continuous & Pulsed Current Rating should exceed peak and continuous current draw in drone (5.5A = 25C * 0.22Ah)

Testing Considerations:

1. Use an oscilloscope to check the PWM signals from the motor gates to see if it is causing sync issues with the motors - ensure consistent PWM frequency across all four motors

2. Test n-channel mosfet Integrity and ensure drain voltage approaches zero as gate voltage increases

Mosfet Testing

Mosfet Testing Probes

3. Test Motor terminals if voltage is received

Motor Terminal Voltage

Practical Considerations:

1. Check NRF24 radio communication first before assembling the drone. Always test parts individually
2. Keep it simple and complexity should not come first. Achieve minimum functionality for initial developments
3. Better to use solder with lead, but prone to contamination (ensure proper storage)
4. Thin kapton tapes do not provide as much insulation as actual electrical tape. Though electrical tape is heavier
5. Ensure the motor power can carry the total load of the drone
6. Ensure prototype works before designing a final PCB

Successful Vendors
------------------
These are the lift of successful vendors that sold the components needed for this project that worked. 

- **Robojax**: Arduino Pro Mini 5V 16MHz 
- **HiLetGo**: NRF24L01+PA+LNA Transeiver Module
- **Aideepen**: NRF24L01 Transeiver Standard Module
- **Aideepen**: Arduino Nano Board
- **Fytoo**: 3.7V 600mAH LiON batteries - used for the controller
- **Fytoo**: 3.7V 220mAH LiON 25C battery
- **WWZMDiB**: Mini USB to TTL Serial Converter Adapter, 3.3V/5.5 V FTDI Breakout Board for Arduino
- **Wishiot**: Thumb Joystick Module Dual Axis Sensor for Arduino
- **DFRobot**: MPU6050 Gyro + Accelerometer Module
- **Digikey**: Surface mount components (resistors, diodes, n-channel MOSFETs, capacitors, etc)
- **Midzooparts**: Lilypad Buzzer Small Speaker Module for Arduino
- **Crazepony**: 4pcs 6x15mm Motor (Speed: Insane) 19000KV, 70000 RPM@3.7V

These are the list of vendors that sold components that did not work or were faulty for this project.

- **Hutomwua**: Arduino Pro Mini 5V 16MHz (Did not meet specifications or seems to be 10MHz on the backside - not advertised)
- **ELEGOO**: Arduno Nano (Faulty and did not program)
- **Fytoo**: 3.7V 1000mAH LiON batteries (potentially drew too much current and burned the board?)
- **Aideepen**: NRF24L01+PA+LNA Transeiver Module (Faulty and did not communicate)

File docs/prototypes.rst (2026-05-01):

.. _prototypes:

Prototypes
===========

This page will provide an overview of the design of the prototypes 
that will start with the initial prototype and the reasons behind the design changes that lead to the next prototype.

Protoype 1
------------

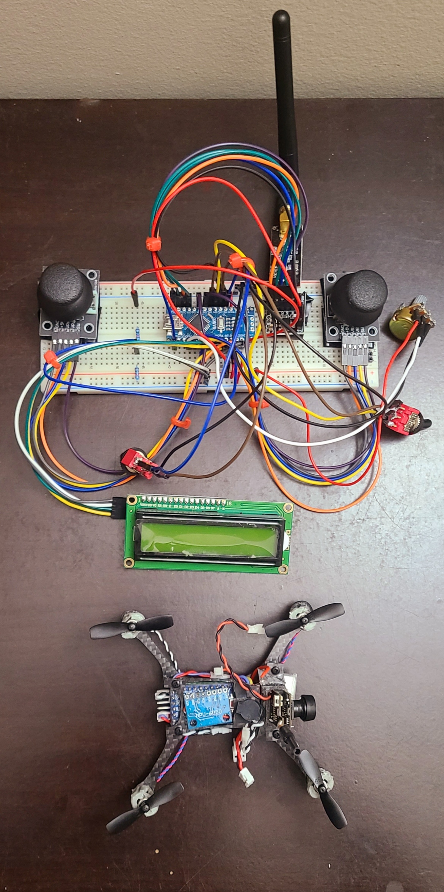
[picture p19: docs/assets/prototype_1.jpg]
Prototype 1


|

The first protoype is the initial attempt at building the NRF24-MultiWii-Drone. However, there were issues in the design that led to failure. 

**The main issues are listed below:**

1. Too heavy
    - Motor fasteners that were improvised using drywall anchors were too heavy (motors will be glued directly in the next prototype)
    - The wires were too thick using 24AWG
    - The perforated board was too large with lots of unused space
    - The soldered JST connectors (NRF24L01, perforated board, buzzer) are too heavy (these will be removed and wires will be soldered directly in the next prototype)
    - 1N5819 diodes are too heavy (using 1N4148 surface mount diodes in the next prototype)
    - Using velcro is too heavy (use super glue instead)

2. Small Propellers/Less Thrust
    - Using 2 blade (faster) 37mm propellers (use 4 blade propellers for more thrust)

3. Conductive Carbon Fiber Frame
    - Possible short circuits when mounted on the carbon fiber frame (use kapton tape for better insulation with the electrical components)

4. Poor Solder Connections
    - Damaged solder tips (oxidized) resulted in poor solder connections with possible decrease in conductivity and connectivity between components and possible short circuits
    - Replace solder tips and properly resolder the connections in the next prototype

5. Need Soldered Controller with Enclosure
    - The controller uses a breadboard with weak connections and unmanaged wiring. Requires a proper enclosure with soldered connections for better reliability

**Additional materials and replacement needed for the next prototype:**

1. Arduino Pro Mini Atmega 328P 5V/16MHz (un-soldered)
2. MPU6050 from DFRobot (un-soldered)
3. Motor Encoder Circuit
    - Surface mount 1N4148 diodes
    - Solder tips + high quality thin solder 
4. Larger 4 blade propellers
5. Kapton tape for insulation
6. Copper Sheet for proper grounding

Protoype 1.1
------------

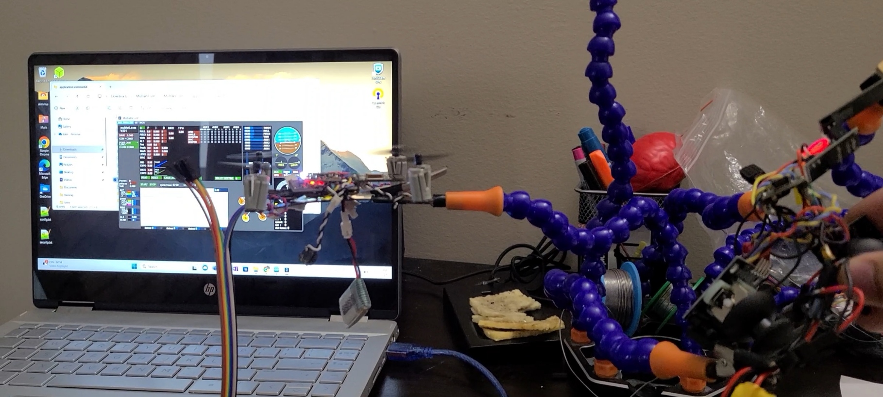
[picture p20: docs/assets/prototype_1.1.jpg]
Prototype 1.1


|

Protoype 1.1 is the second attempt at building the NRF24-MultiWii-Drone. However, there were still issues in the design that led to failure. 

**The main issues are listed below:**

1. Kapton Tape did not provide proper insulation
    - After adding one layer of kapton tape, it seemed that the electrical components, mainly the IMU shorted and was damaged. This resulted in the accelerometer unable to properly register the movements in MultiSim. The next prototype will include a proper enclosure for the electrical components of the drone. Although the main frame will still be carbon fiber, a separate box enclsoure will be used to cover the electrical components properly using light materials
    - Furthermore, investigating the use of hot glue for proper insulation. However, initial research suggests this may lead to further design failures

2. Controller is Too Complex
    - "Simplicity is the ultimate sophistication." - Leonardo da Vinci 
    - Unnessary components in the controller atleast for the MVP such as the 16x2 LCD to track voltage and the potentiometer should be removed. The controller should be simplified to only include the basic components needed for communicating with the drone and this includes the Arduino Nano controller, the radio module + PA + LNA components, the two joysticks, the two SPDT switches, and the SPST switch with the 3.7V batteries

3. Controller Battery has too much current
    - Prolonged use of the controller lead to overheating of the components and controller failure. Theory is that the battery packs too much current which the components could not handle resulting in breakdown. The two batteries are connected in series are 3.7V 1000mAH. Looking into the use of 3.7V and 600mAH batteries instead

4. Remove the Grounded Copper Sheet
    - This may not be needed as I have not encountered any issues with the drone resetting. This solution was suggested online, but I should not implement solutions to problems that does not exist in my design

**Additional materials and replacement needed for the next prototype:**

1. Arduino Pro Mini Atmega 328P 5V/16MHz (un-soldered)
2. Arduino Nano 
3. Radio Modules NRF24L01 + PA + LNA
4. 3.7V 600mAH batteries (2x)

Prototype 1.2
-------------

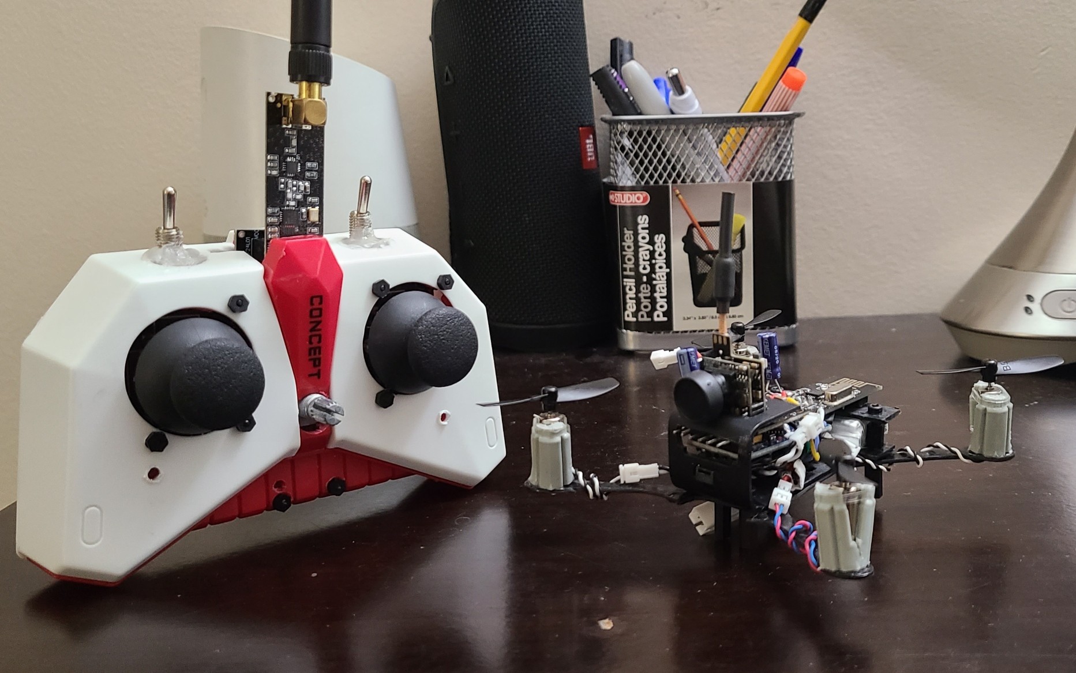
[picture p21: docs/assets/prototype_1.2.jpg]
Prototype 1.2


|

Prototype 1.2 is the third attempt at building the NRF24-MultiWii-Drone. This prototype addresses the issues found in the previous prototypes and introduces new design elements.
The primary issue in this prototype is that the motors do not respond despite the joystick movements being translated in MulitSim. The drone keeps resetting and attempts to calibrate. 

**The possible issues are listed below:**

1. The battery discharge rate is too low (25C) and that a proper drone battery with a higher discharge rate (30C or higher) is needed
    - Recommended to use "Turnigy Nano-Tech" batteries or similar for their high performance
2. The power for the radio is not consistent and requires a 10uF filtering capacitor at the NRF24 power inputs
3. The power for the Arduino Pro Mini is not consistent and requires a 100uF filtering capacitor
    - Confirm Arduino Pro Mini 3.3V 8MHz, or 5V 16MHz is required
    - Research shows that Arduino Pro Mini 5V 16MHz is recommended to be compatible with MultiSim
4. The power lines has a large AWG (small thickness) where the current cannot be supplied properly
    - Recommended to use solder with lead and keep solder enclosed after use to avoid contamination/oxidation
    - For the motor driver, ensure the proper components are rated for this circuit
    - These components are being used but requires confirmation; 0603 10K SMD resistor 103, SI2300DS-T1-GE3CT-ND N-Channel Mosfet 30V 3.6A, 1N4148 diode surface mount
5. Motor PWM signals could be too weak to drive the motors
    - Requires oscilloscope to confirm suspicion
    - This factor can be set in the MultiWii software, `float adjustmentFactor` on line 1069 of output.cpp
6. Potential EMF noise or leaks is affecting the IMU readings? 
7. The Arduino Pro Mini is faulty which was purchased from "Hutomwua". The previous prototypes was working which was purchased from "Robojax"

**Additional materials and replacement needed for the next prototype:**

1. Arduino Pro Mini Atmega 328P 5V/16MHz (un-soldered) from Robojax specifically

Prototype 1.3
-------------

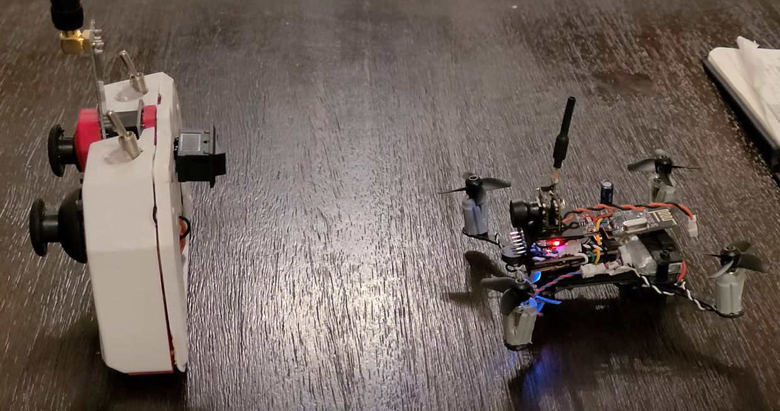
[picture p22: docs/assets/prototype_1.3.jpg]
Prototype 1.3


|

Prototype 1.3 is the fourth attempt at building the NRF24-MultiWii-Drone. This prototype was successful in motor response from the controller movements. 
However, there were still issues where the drone movements were erratic and unstable. There is enough motor throttle to lift the drone, but the drone was unable to
properly lift due to instability and lack of motor synchronization.

**The possible issues are listed below**

1. The drone is not calibrated properly
    - The drone needs to sit on a flat surface for a proper calibration
    - The accelerometer and the gyroscope needs proper calibration
    - Adjust settings in MultiWii configuration with max smoothness
2. Motor direction is wrong
    - This can be verified by feeling if the air is being pushed upwards
    - Record slow motion video to see the direction of the motors
3. The motor RPMs are not the same and unsynchronized
4. The forward direction of the MPU6050 is in the opposite direction
    - Rewire orientation of the motors to have face the MPU6050 in its forward direction
5. The drone is still too heavy and certain weights of the components are not balanced causing the center of gravity to be offset
    - Remove heavy motor mounts and just rely on superglue to attach the motors
6. The arms of the drone are limble which causes wobbling during flight
    - Reinforce the arms with a stronger material that doesn't bend such as popsicle sticks

Prototype 1.4
-------------

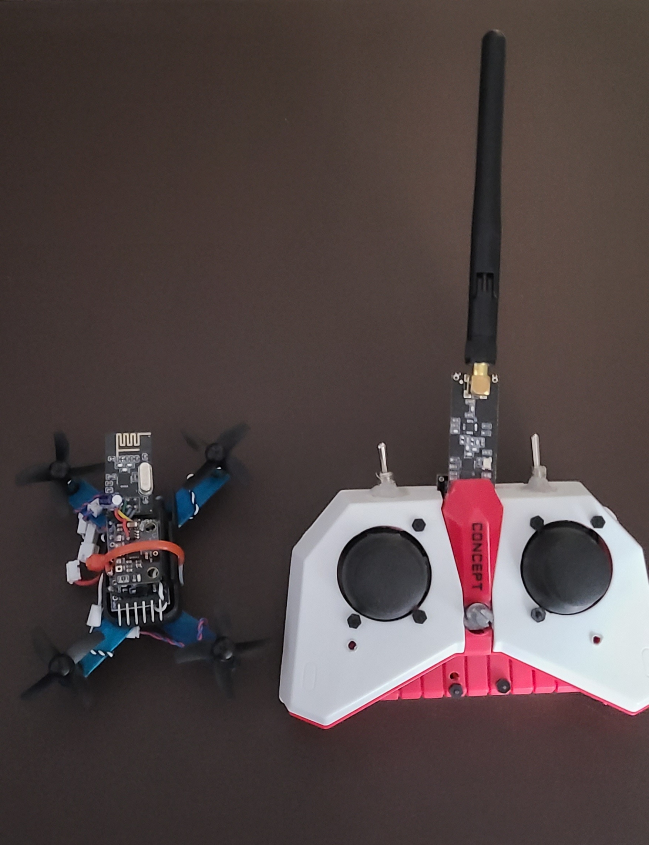
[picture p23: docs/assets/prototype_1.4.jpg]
Prototype 1.4


|

Prototype 1.4 is the fifth attempt at building the NRF24-MultiWii-Drone. This prototype still could not fly despite the design changes 
to the frame. The motor direction has been corrected; top left => clockwwise, top right => counter-clockwise, bottom left => counter-clockwise, bottom right => clockwise.
The drone motors are now super glued onto the arms and the arms have been converted into popsicle sticks which does not bend easily. Furthermore, the drone has been made smaller,
though it did decrease the overall surface area of the drone, much of the weight has been reduced. Lastly, an EMF blocking shield made of copper has been
attached in the underside of the Arduino Pro Mini to reduce possible interference with the motor controller. PID tuning has also been explored and adjusted,
but still could not find the right values for a stable flight.

**The possible issues are listed below**

1. IMU wobbles, unsecure mount
2. Frame is yet still too heavy
3. Smaller propellers + arm surface area - more unstable
4. Battery is mounted at the bottom which makes it hard to connect
5. Wrong drone output behaviour from the joystick movements - needs software correction
6. Needs PID tuning for the roll, pitch, and yaw

The current configurations with the expected behaviour and the actual behaviour are noted below.

Prototype 1.4 Configuration

**Design changes for the next prototype**

1. Software correction to the motor behaviour
2. Configure joystick values for correct controller calibration
3. Lighter frame, longer arms, secure mounts
4. Proper PID tuning for the drone's roll, pitch, and yaw

Prototype 1.5
-------------

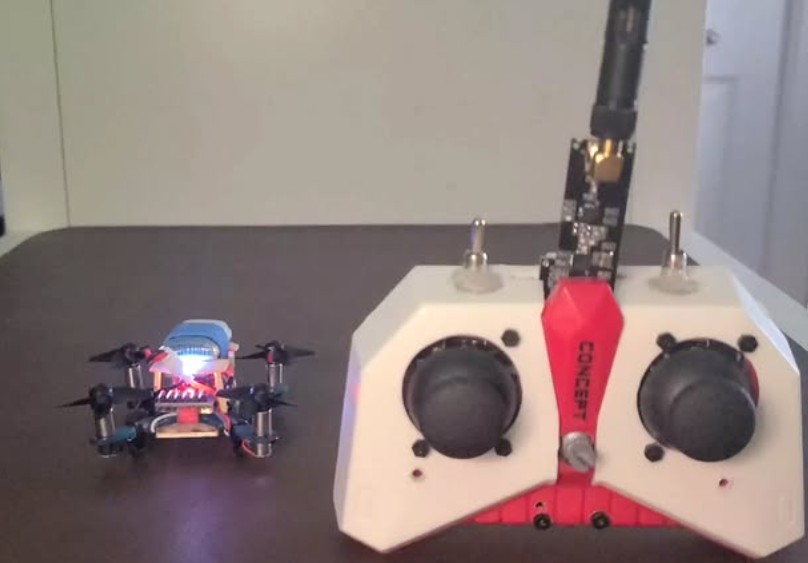
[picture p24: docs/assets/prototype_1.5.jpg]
Prototype 1.5


|

Prototype 1.5 is the sixth attempt at building the NRF24-MultiWii-Drone. This version is still unable to lift off due to major instabilities in 
the flight pattern. For instance, the joystick movements don't seem to match the drone behavior. The drone motors seem to be out of 
sync (PWM signals need to be looked at closely). Furthermore, the drone does keep resetting from time to time. The drone might need PID tuning 
and joystick value adjustments.

**The possible issues are listed below**

1. Motor driver components are too close to the controller (large EMF effects)
2. All power is drawn from the same source connected to the VCC pin of the Arduino Pro Mini
3. Wire thickness used is 28AWG (from 1.25mm connector sockets) - should be 30AWG+
4. The incorrect translation from the controller joystick movements to the drone motor behaviour is causing instability
5. IMU is not sitting flat and unstable
6. Drone motors are not positioned evenly
7. Frame is still too heavy
8. Small surface area drone causing instability

**Design changes for the next prototype**

1. Placement of motor driver components on the arms to disperse combined EMF effects and reduce interference with the controller
2. Power should be directly towards raw pin, VCC, or both?
3. Convert the drone to a PCB to have solid connections between components and reduce the weight from the wires
4. PWM drone pins should be consistent with Electronoobs: FR (D6), BR (D9), BL (D5), FL (D3)

Prototype 2.0
-------------

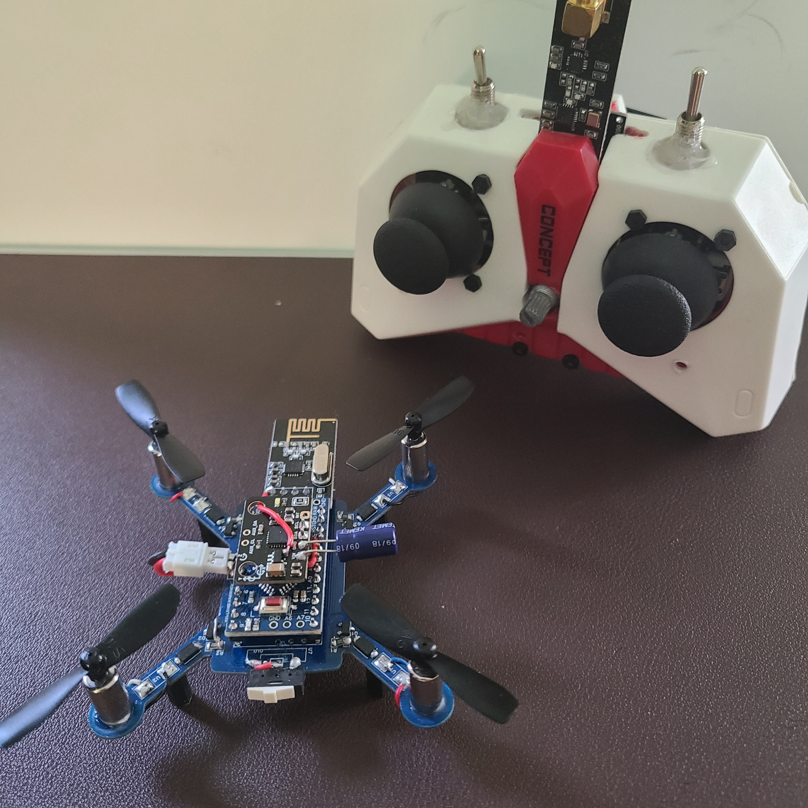
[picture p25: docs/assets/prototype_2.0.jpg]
Prototype 2.0


|

Prototype 2.0 is the seventh attempt at building the NRF24-MultiWii-Drone. This prototype is based on a PCB design using EasyEDA and manufactured by JLCPCB. 
The PCB is designed to be its own frame and has the components soldered directly onto the board. There were component changes to the motor driver based on the following characteristics:

- 10KOhm resistor 0805 (0.125W)   `CRG0805F10K <https://www.digikey.ca/en/products/detail/te-connectivity-passive-product/CRG0805F10K/2380831>`_
    * Ensures VGS = 0
- Diode: `SS54FSH <https://www.digikey.ca/en/products/detail/taiwan-semiconductor-corporation/SS54FSH/18718584>`_ (5A, 40V)
    * Maximum rated current must be greater than 2 * stall current (assuming 2-6A)
- N- Channel Mosfet: `AO3400A <https://www.digikey.ca/en/products/detail/alpha-omega-semiconductor-inc/AO3400A/1855772>`_ or `AO3416 <https://www.digikey.ca/en/products/detail/alpha-omega-semiconductor-inc/AO3416/1855783>`_
    * VDS ~>20-30V is better (rated for high voltage spikes)
    * RDS ~<10mOhm is better (low power loss)
    * Gate threshold ~2.5-3.3V (turns on based on battery capacity)
    * Continuous & Pulsed Current Rating should exceed peak and continuous current draw in drone (5.5A = 25C * 0.22Ah)

The previous components had the following limitations:

- 10KOhm resistor 0603 (0.1W, 2.A max current)
    - Low power and current rating
- 1N5819/1N4148 - Used: 1N4148WS-13-F  (Consider using 1N5819 for low voltage drops)
    - 1N5819: Low voltage drop (~0.3-0.4V)
    - 1N4148: Fast switching, but higher voltage drop (~0.7V)
    - Current rating must be greater than 2 * stall current (2-6A assuming)
- S12300 n-mosfet - Used: SI2300DS-T1-GE3CT-ND

Despite the component changes and the PCB design, the drone still could not lift off and behaves even more poorly. At certain times the current drawn from the back right motor is so high that it is the only motor spinning very fast.
When I disconnect the back right motor, the rest of the motors spins, but then the reset issue persists despite the motor drivers placed at the arms. It seems that dividing the motor driver at the arms does not reduce the EMF effects on 
the Arduino Pro Mini. 

Prototype 2.1
-------------

Prototype 2.1

|

Prototype 2.1 is the eight attempt at building the NRF24-MultiWii-Drone. This prototype is based on the same PCB design as Prototype 2.0, but with component changes to the motor driver and other design changes to address the issues found in Prototype 2.0.
This drone was able to lift off, but the flight is still quite unstable. Here are the design choices that made drastic improvements.

- revert to components 1N4148 Diode, S12300DS n-Mosfet, 10KOhm 0805 resistor
- place copper shield between motor drivers and the Atmega328P/MPU6050 for EMF shielding
- thicker (0.45-0.50mm) power lines, zero 90 degree traces, similar power lengths
- 10uF capacitor at the NRF24L01 power pins
- 100uF capacitor at the MPU6050 power pins
- 3.7V 30C 450mAH battery (minimum 25C)
- consistent motor placement - wiring needs to be at the same start rotation
- Minthrottle is set to 1050 based on the comment description "for brushed ESCs like ladybird"
- larger propellers -> larger surface area -> bigger lift

The importance of capacitors at the power pins:

1. No capacitor -> unable to throttle down (motors keeps spinning) - looks like loss of signal at the NRF24L01 module
2. 10uF capacitor at the NRF24L01 power inputs - motors become out of sync - maybe loss of power at the motor terminals
3. 100uF capacitor at the MPU6050 - only the back left motor is not spinning
4. 100uF capacitor at the microcontroller - no change from previous point
5. 470uF capacitor at the battery terminals - front left and back left motors no longer spin

Turns out problems (3-5) are due to the motors burning out from problem 1 which caused overworking in the motors potentially burning inside components.

The biggest change was remapping the motor designations in the software output.cpp based on the following comparisons to various projects and pin designations.

+-----------+----------------------+---------------------------------+---------------+------+--------------+
| Motor     | Intended Orientation | Max Imagination (Current Setup) | Electronoobs  | Code | Test Results |
+===========+======================+=================================+===============+======+==============+
| Motor[0]  | BR                   | D3                              | D9            | D9   | FR           |
+-----------+----------------------+---------------------------------+---------------+------+--------------+
| Motor[1]  | FR                   | D9                              | D6            | D6   | FL           |
+-----------+----------------------+---------------------------------+---------------+------+--------------+
| Motor[2]  | BL                   | D5                              | D5            | D5   | BL           |
+-----------+----------------------+---------------------------------+---------------+------+--------------+
| Motor[3]  | FL                   | D6                              | D3            | D3   | BR           |
+-----------+----------------------+---------------------------------+---------------+------+--------------+

It seems that the code matches Electronoobs setup. Since I have followed Max Imaginations PWM wirings, I have to modify the software to reflect this wiring. 

Thus the software needs to match the following configuration.

* Motor[0] => FR
* Motor[1] => FL
* Motor[2] => BL
* Motor[3] => BR

So the following lines in output.cpp was modified to:

**Before**

.. code-block:: shell

    motor[0] = PIDMIX(-1,+1,-1); //REAR_R
    motor[1] = PIDMIX(-1,-1,+1); //FRONT_R
    motor[2] = PIDMIX(+1,+1,+1); //REAR_L
    motor[3] = PIDMIX(+1,-1,-1); //FRONT_L

**After**

.. code-block:: shell
    
    motor[0] = PIDMIX(-1,-1,+1); //FRONT_R
    motor[1] = PIDMIX(+1,-1,-1); //FRONT_L
    motor[2] = PIDMIX(+1,+1,+1); //REAR_L
    motor[3] = PIDMIX(-1,+1,-1); //REAR_R

After these changes, I still face issues with poor motor response at the front left motor. Though it spins sometimes and allows the drone to liftoff, it does lose its spin from time to time. 
I will try to make these design changes to improve the response.

1. Reinforce connections with external wiring for the front left motor
2. Experiment with various PID values to see if it improves the motor response and stability of the drone
3. Try to add a capacitor at the NRF24L01 power pins of the controller to see if it improves the signal strength and response of the drone

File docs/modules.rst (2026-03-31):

NRF24-MultiWii-Drone
====================

.. toctree::
   :maxdepth: 4

   intro
   drone_tutorial
   controller_tutorial
   prototypes
   reflection
   future

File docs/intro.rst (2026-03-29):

.. contents::
   :local:
   :depth: 2

Introduction
=============

This documentation provides an overview of the NRF24 MultiWii Drone project, including its design, components, and step-by-step tutorials for building both the drone and its controller.
It is structured to help users understand the project from its initial concept to the final assembly, including the challenges faced and solutions implemented in various prototypes.

To learn more about the different parts of the project, explore the sections below:

1. **Drone Tutorial**  
   Learn more about the step-by-step tutorial for building the NRF24 MultiWii Drone.  
   See the full guide in the :ref:`Drone Tutorial <drone_tutorial>` section.

2. **Controller Tutorial**  
   Learn more about the step-by-step tutorial for building the NRF24 MultiWii Drone Controller.  
   Check out the complete guide in the :ref:`Controller Tutorial <controller_tutorial>` section.

3. **Prototypes**  
   Learn more about the various prototypes and design changes of the drone.  
   See the full details in the :ref:`Prototypes <prototypes>` section.

4. **Reflection**  
   See the personal reflection on the project, including the motivation, challenges, and lessons learned.  
   Read the full reflection in the :ref:`Reflection <reflection>` section.

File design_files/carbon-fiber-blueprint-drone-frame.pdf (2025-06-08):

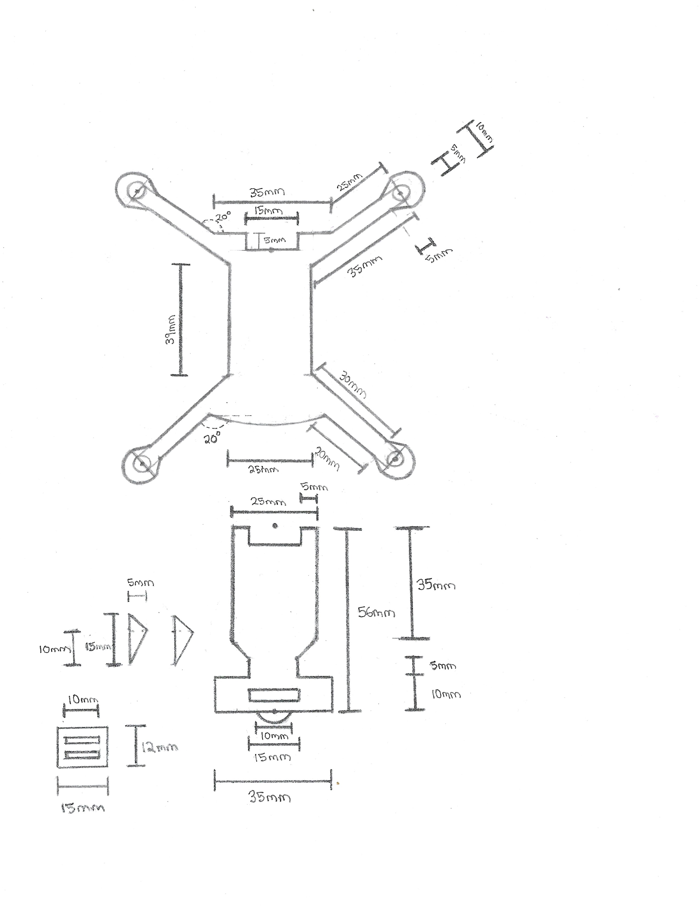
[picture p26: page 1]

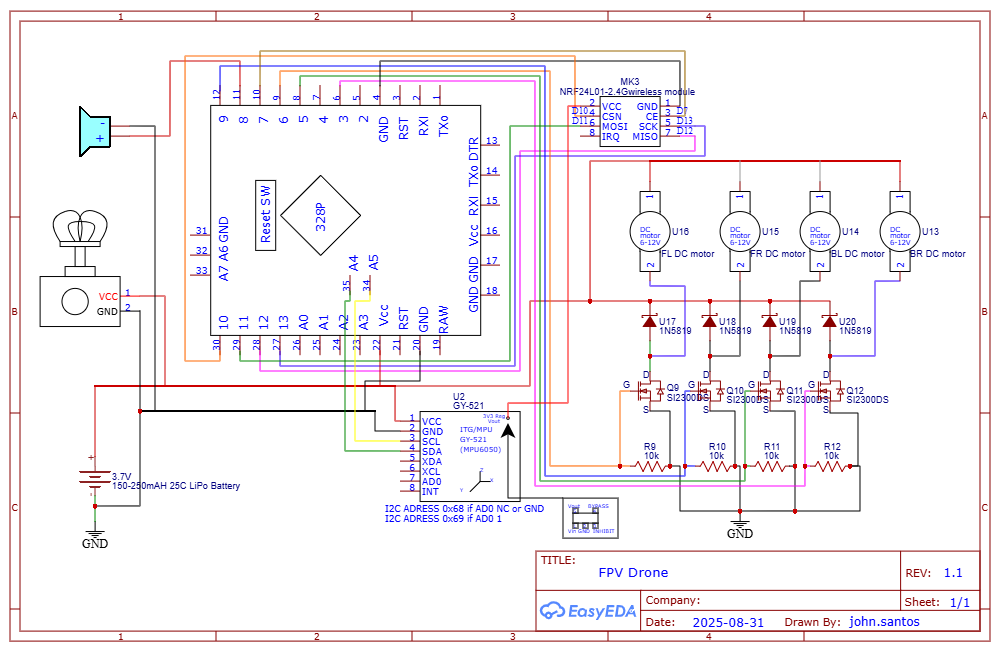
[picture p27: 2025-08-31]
docs/assets/schematic_drone.png

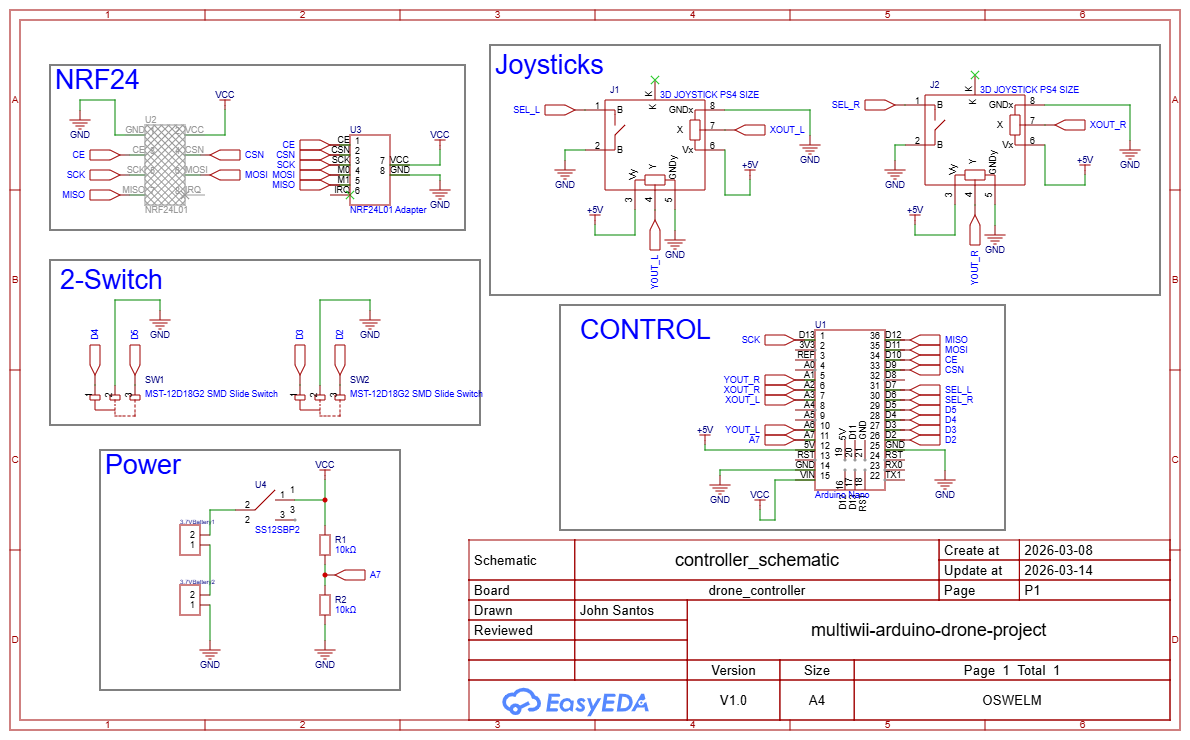
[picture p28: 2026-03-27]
docs/assets/SCH_controller_schematic_1-P1_2026-03-26.png

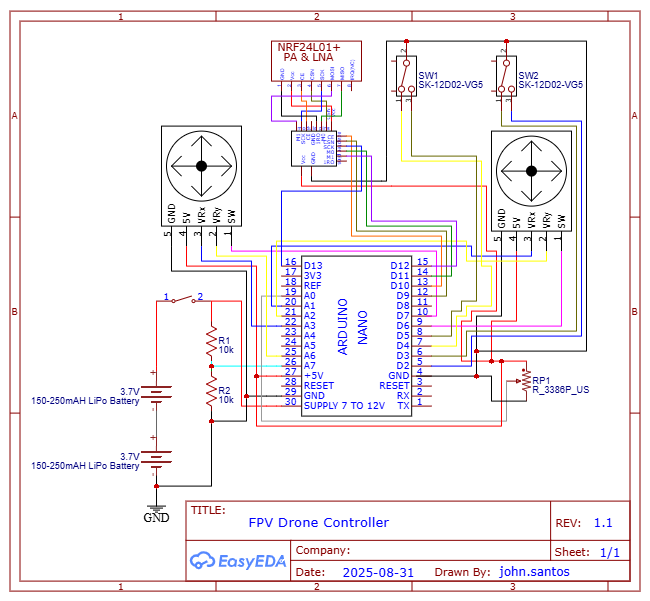
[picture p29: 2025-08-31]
docs/assets/schematic_controller.png

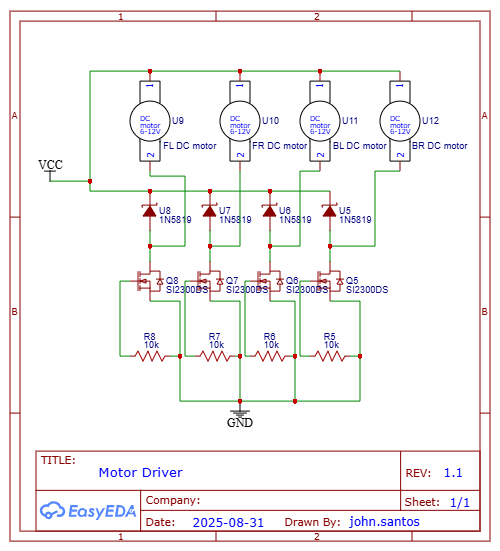
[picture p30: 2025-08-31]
docs/assets/schematic_motor_driver.png

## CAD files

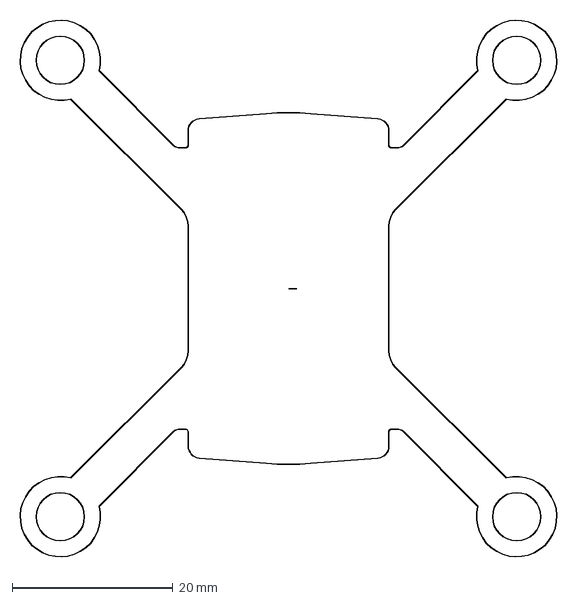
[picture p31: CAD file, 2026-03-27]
design_files/drone_sketch.dxf
67.7 x 67.7 mm

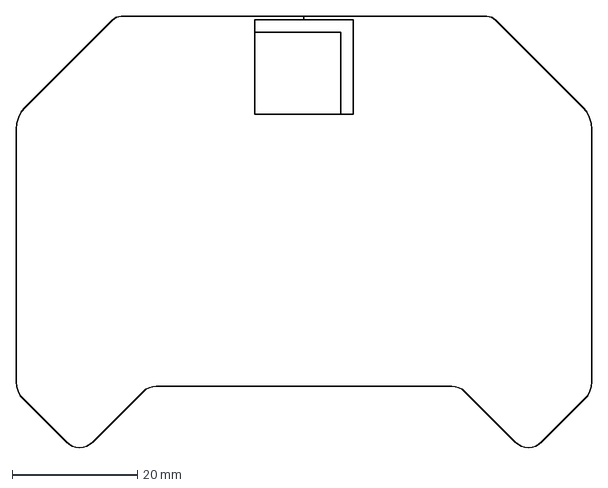
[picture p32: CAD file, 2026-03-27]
design_files/controller_sketch.dxf
91.8 x 68.8 mm

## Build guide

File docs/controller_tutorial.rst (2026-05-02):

.. _controller_tutorial:

Controller Tutorial
====================

This page will show the step-by-step tutorial for building the NRF24 MultiWii Drone Controller.

Materials
##########

1. Arduino Nano Atmega328P 3V (x1)
2. NRF24L01+PA+LNA Transceiver Module with 8-pin Breakout Adapters (x1)
3. Joystick Module for Arduino Dual Axis Sensor (x2)
4. 3-pin Switch (x2)
5. Power Switch (x1)
6. Power Connector (x2)
7. Charging Connector (x1)
8. 3.7V LiPO Battery 600mAH (x2)

Frame
#######

The controller frame is from an `RC 3 wheel stunt car <https://www.mindgames.ca/rc-sinovan-3-wheel-stunt-car-2-4g-mutilcolor/>`_ which was modified 
to fit the electrical components of this drone controller. 

.. list-table::
   :widths: 50 50
   :header-rows: 0

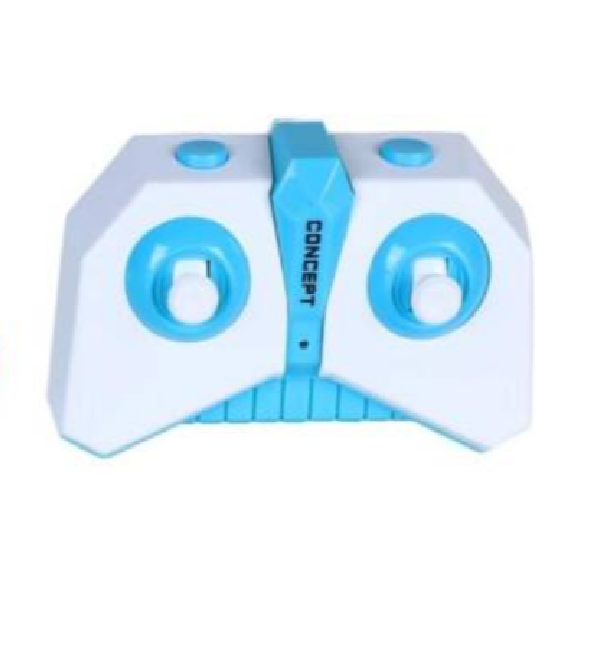
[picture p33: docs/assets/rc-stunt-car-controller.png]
RC Stunt Car Controller
   * - 
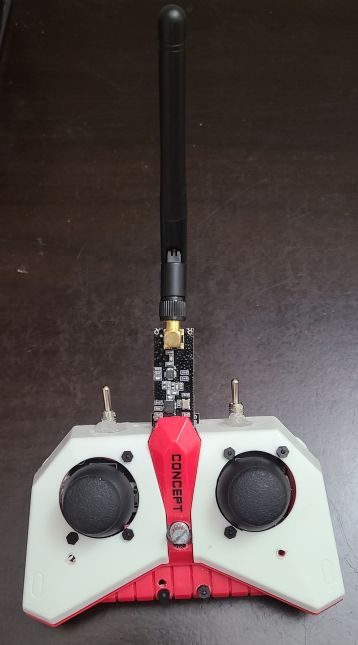
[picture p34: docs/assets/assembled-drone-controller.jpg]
Assembled Drone Controller
     - 

Electrical
#############

1. If you choose to assemble to PCB, you can take the Gerber files for the controller PCB and upload them to JLCPCB to manufacture the PCB. The Gerber file can be found in the `design_files/Gerber_Controller_PCB_v2.1_2026-05-01.zip`. Otherwise, you can proceed with the next steps for the alternative method.

2. Assemble and solder the electrical components based on this schematic diagram.

Controller Circuit Schematic

3. The assembled controller circuit should look like the following.

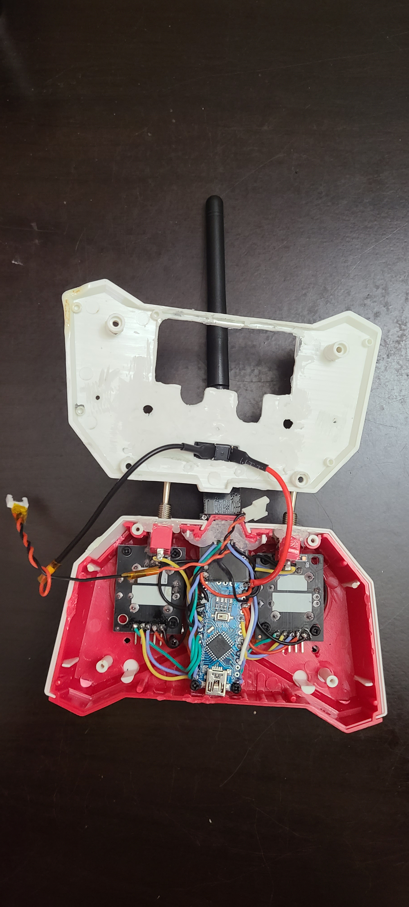
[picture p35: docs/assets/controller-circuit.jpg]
Controller Circuit


Software
##########

1. Open the Arduino IDE and open the project `MultiWii_RF24`.

2. Install the following libraries and include the ZIP libraries in the Arduino IDE.

* `RF24 <https://electronoobs.com/eng_arduino_NRF24_lib.php>`_
* `TimerFreeTone_v1.5 <https://bitbucket.org/teckel12/arduino-timer-free-tone/downloads/TimerFreeTone_v1.5.zip>`_

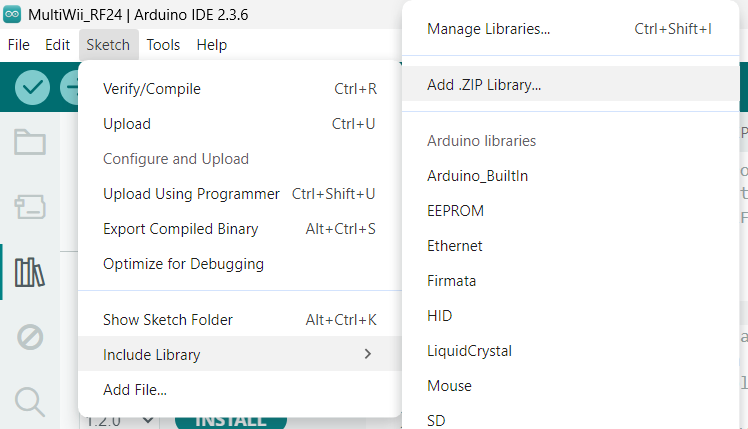
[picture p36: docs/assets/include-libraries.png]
Arduino Include Libraries


3. Adjust the upload settings in Arduino under Tools to set the right board "Arduino Nano", the COM Port, and the processor to "ATmega328P (Old Bootloader)".

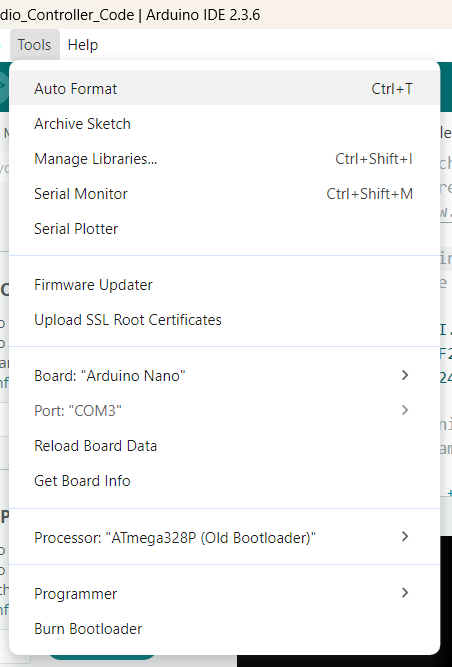
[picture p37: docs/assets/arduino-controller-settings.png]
Arduino Controller Settings


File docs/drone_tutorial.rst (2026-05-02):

.. _drone_tutorial:

Drone Tutorial
===============

This page will show the step-by-step tutorial for building the NRF24 MultiWii Drone.

Materials
##########

1. Arduino Pro Mini Atmega328P 5V/16MHz (x1)
2. MPU6050 Gyroscope/Accelerometer from DFRobot (SEN0142) (x1)
3. NRF24L01+ Transceiver Module (x1)
4. Lilypad 5V Buzzer Speaker (x1)
5. Micro 600TVL FPV Camera with 5.8GHz 25mW Transmitter (x1)
6. 6x15mm 0.8mm Shaft Coreless Motors 19000KV (x4)
7. `1N4148 <https://www.digikey.ca/en/products/detail/diodes-incorporated/1N4148WS-7-F/815127>`_ Surface Mount Diode (x4)
8. `Si2300DS <https://www.digikey.ca/en/products/detail/vishay-siliconix/SI2302CDS-T1-E3/2345137>`_ Surface Mount N-Channel MOSFET (x4)
9. `CRG0805F10K <https://www.digikey.ca/en/products/detail/te-connectivity-passive-product/CRG0805F10K/2380831>`_ 10KOhm Surface Mount Resistor (x4)
10. 2 Blade 37mm Propellers (x4)
11. LiPO Battery 3.7 450mAH (30C) + charger + JST Battery Connector (x1)

Common
---------

1. 30AWG Wires
2. Super Glue
3. Soldering Iron and Solder
4. Mini USB to TTL Serial Converter Adaptor
5. M2 Nylon Hex Spacer Standoff Kit with Male and Female Screw Nut etc.
6. FPV Goggles

Hardware
#############

1. Take the Gerber files for the drone PCB and upload them to JLCPCB to manufacture the PCB. The Gerber file can be found in the `design_files/Gerber_Drone_PCB_v2.1_2026-05-01.zip` 

2. The drone PCB is based off the following schematic.

Drone Circuit Schematic

3. The PCB should appear as the following when it is received.

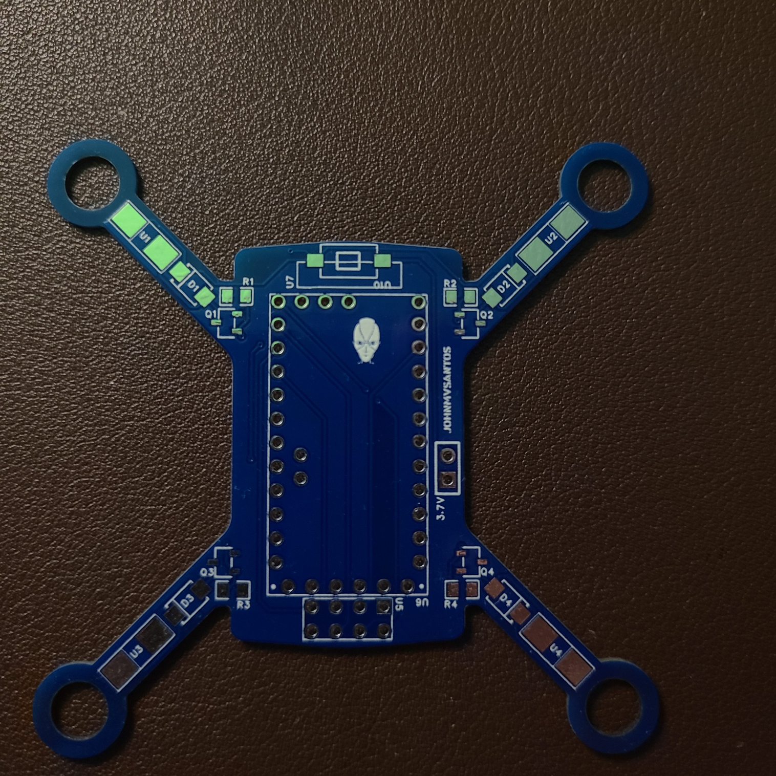
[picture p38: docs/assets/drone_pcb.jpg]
Drone PCB


4. Assemble and solder the motor driver of the drone along the arms with 10KOhm resistor 0805, 1N4148 surface mount diodes, and Si2300DS N-channel Mosfets.

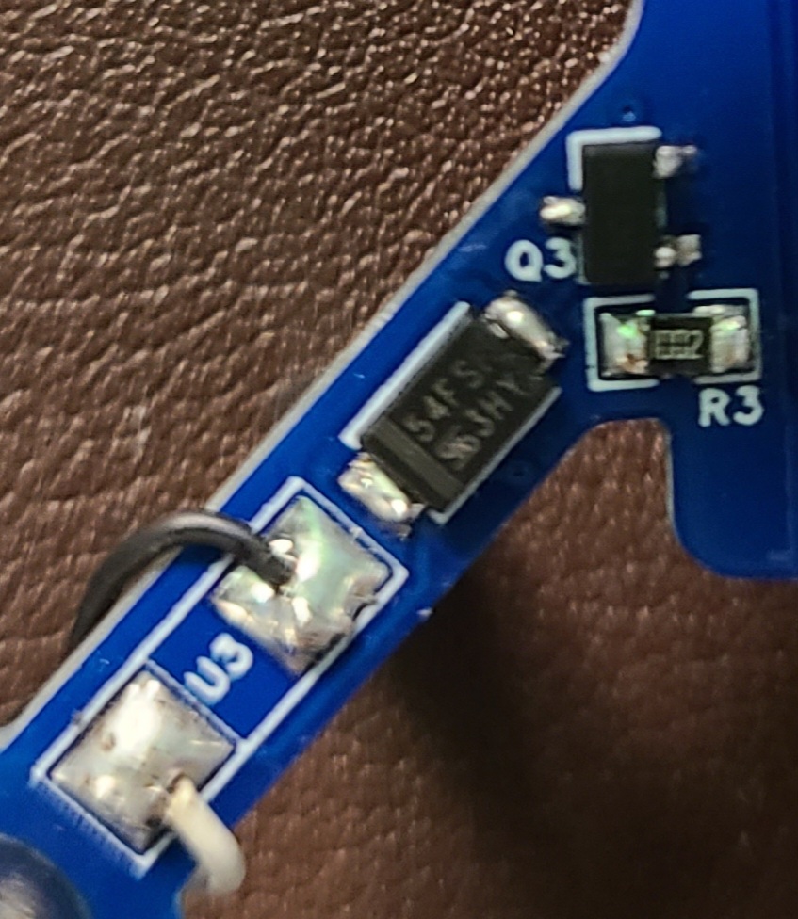
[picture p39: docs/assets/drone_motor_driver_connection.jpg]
Drone Motor Driver Connections


5. Solder the NRF24L01+ Transceiver Module.

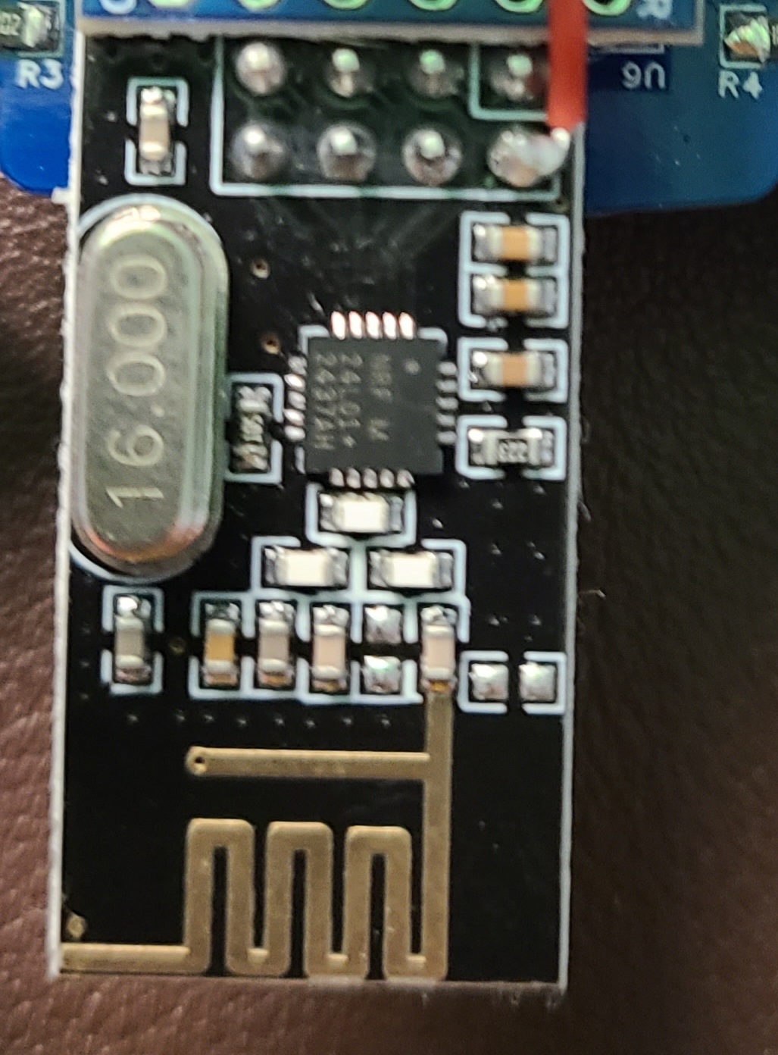
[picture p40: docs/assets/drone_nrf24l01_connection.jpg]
Drone NRF24L01 Connections


6. Solder the switch and the buzzer to the PCB.

.. list-table::
   :widths: 50 50
   :header-rows: 0

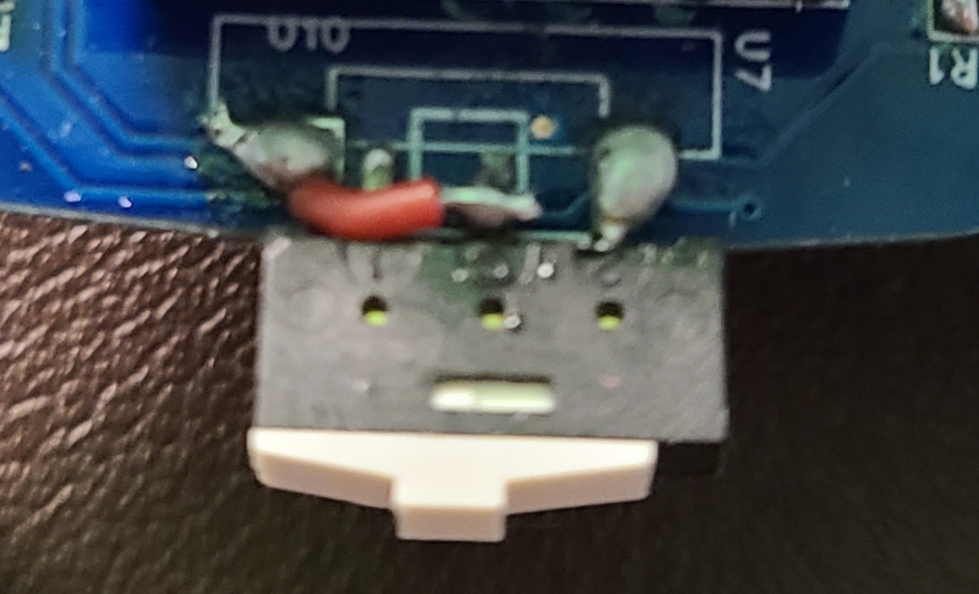
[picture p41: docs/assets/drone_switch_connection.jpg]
Switch Connection
   * - 
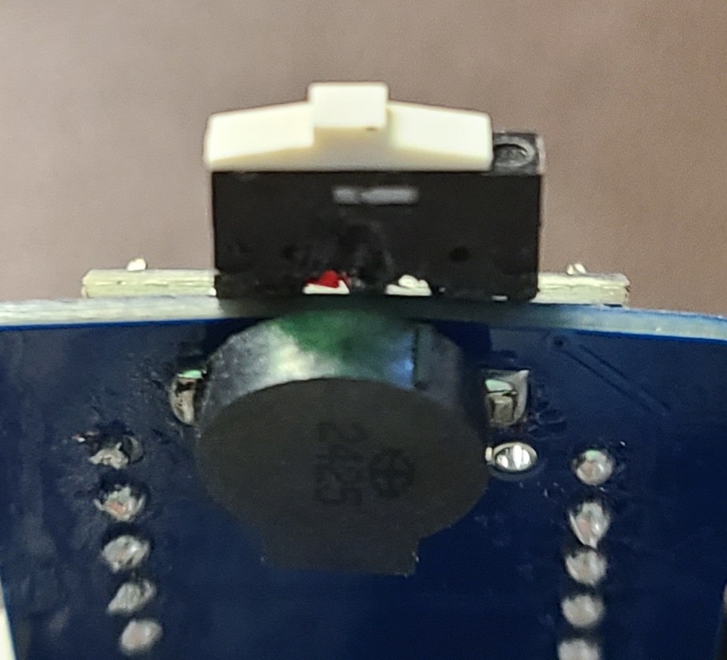
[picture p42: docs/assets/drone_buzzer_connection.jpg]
Buzzer Connection
     - 

7. Solder the Arduino Pro Mini to the PCB.

8. Solder the MPU6050 on top of the Arduino Pro Mini. Solder the power connections of the MPU6050 and the NRF24L01.

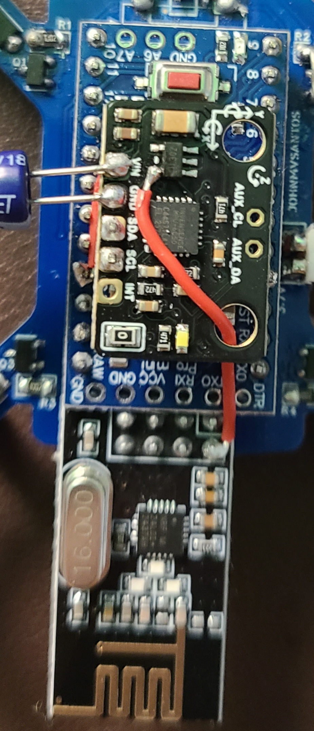
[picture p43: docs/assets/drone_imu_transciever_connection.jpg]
Drone MPU6050 and NRF24L01 Connections


9. The final assembled drone should look like the following.

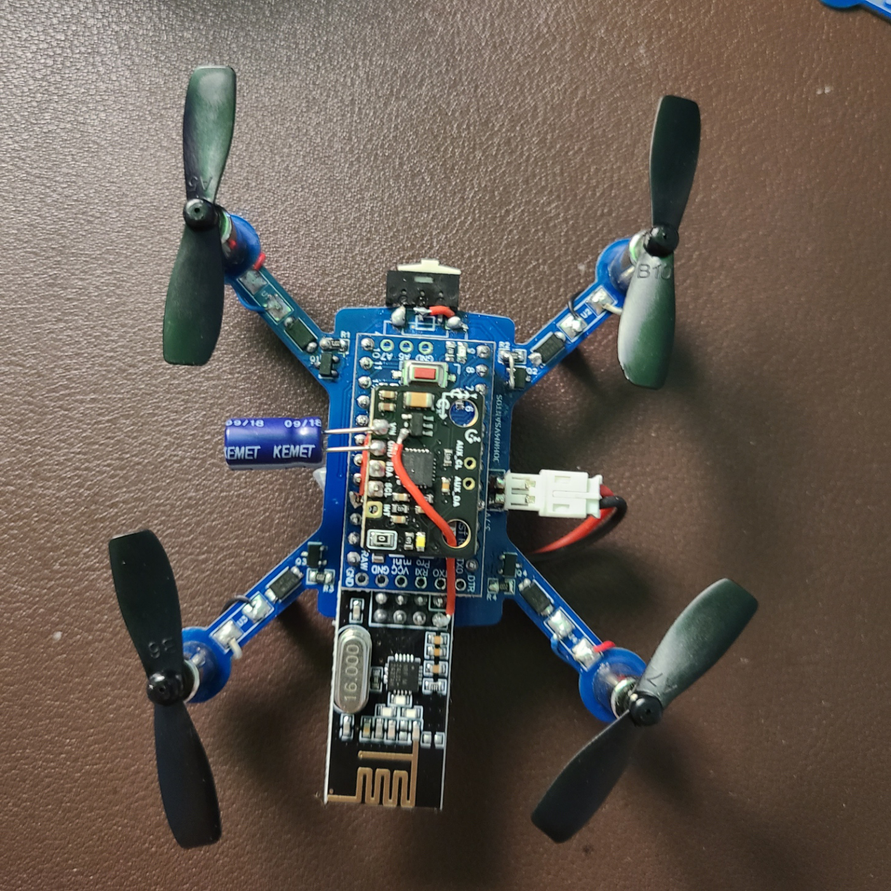
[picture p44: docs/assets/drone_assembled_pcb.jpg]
Drone Assembled PCB


Software
##########

1. Open the Arduino IDE and open the project `MultiWii_RF24`.

2. Install the following libraries and include the ZIP libraries in the Arduino IDE.

* `RF24 <https://electronoobs.com/eng_arduino_NRF24_lib.php>`_
* `TimerFreeTone_v1.5 <https://bitbucket.org/teckel12/arduino-timer-free-tone/downloads/TimerFreeTone_v1.5.zip>`_

Arduino Include Libraries

3. Adjust the upload settings in Arduino under Tools to set the right board "Arduino Pro or Pro Mini", the COM Port, and the processor to "ATmega328P (5V, 16MHz)".

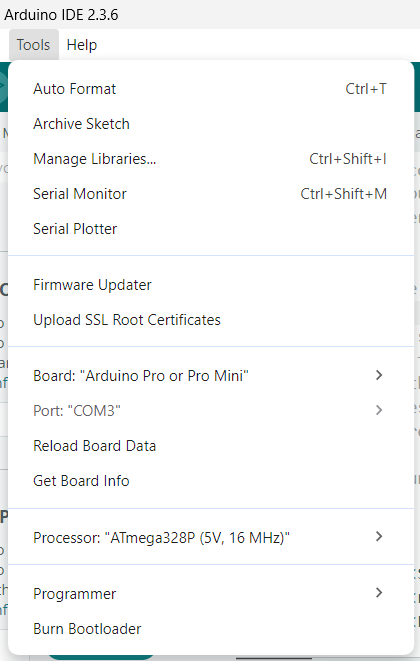
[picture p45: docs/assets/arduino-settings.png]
Arduino Settings


4. Upload the software to the Arduino. Ensure to reset the Arduino once the programming stage reaches this state.

Hit Reset

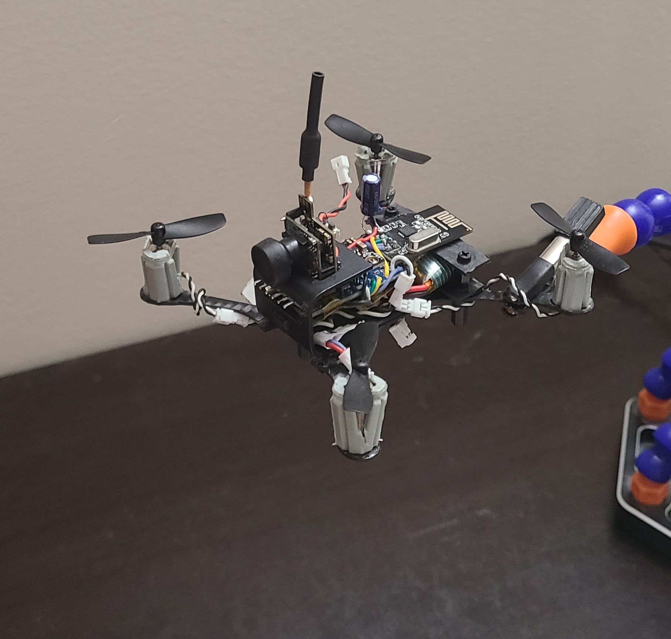
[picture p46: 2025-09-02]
docs/assets/drone-assembled.jpg

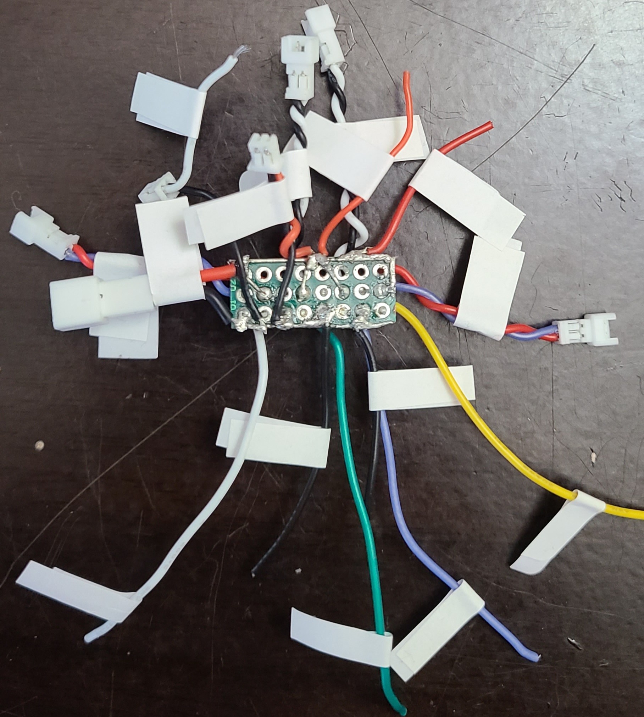
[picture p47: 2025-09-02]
docs/assets/assembled-motor-driver-backside.jpg

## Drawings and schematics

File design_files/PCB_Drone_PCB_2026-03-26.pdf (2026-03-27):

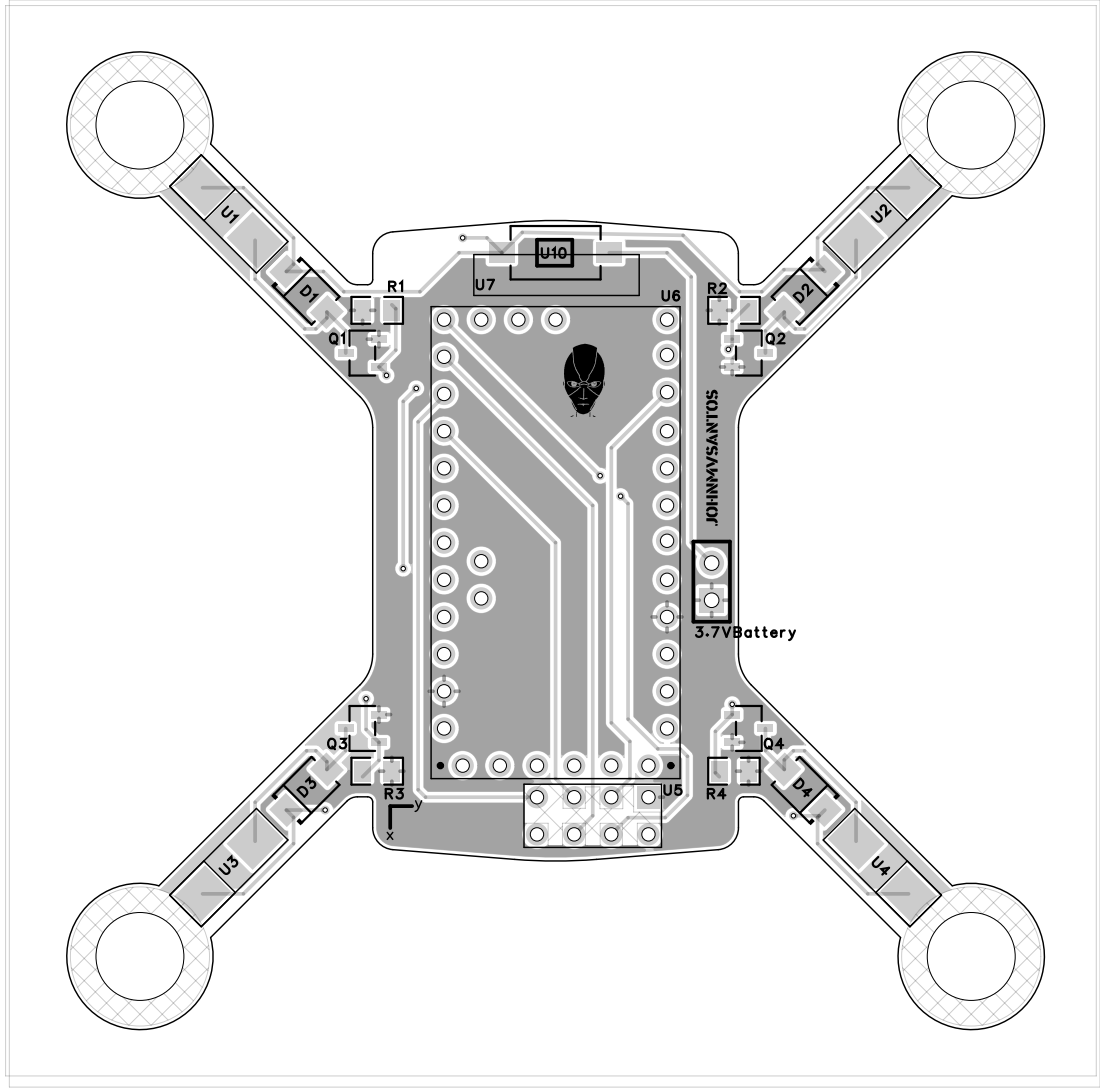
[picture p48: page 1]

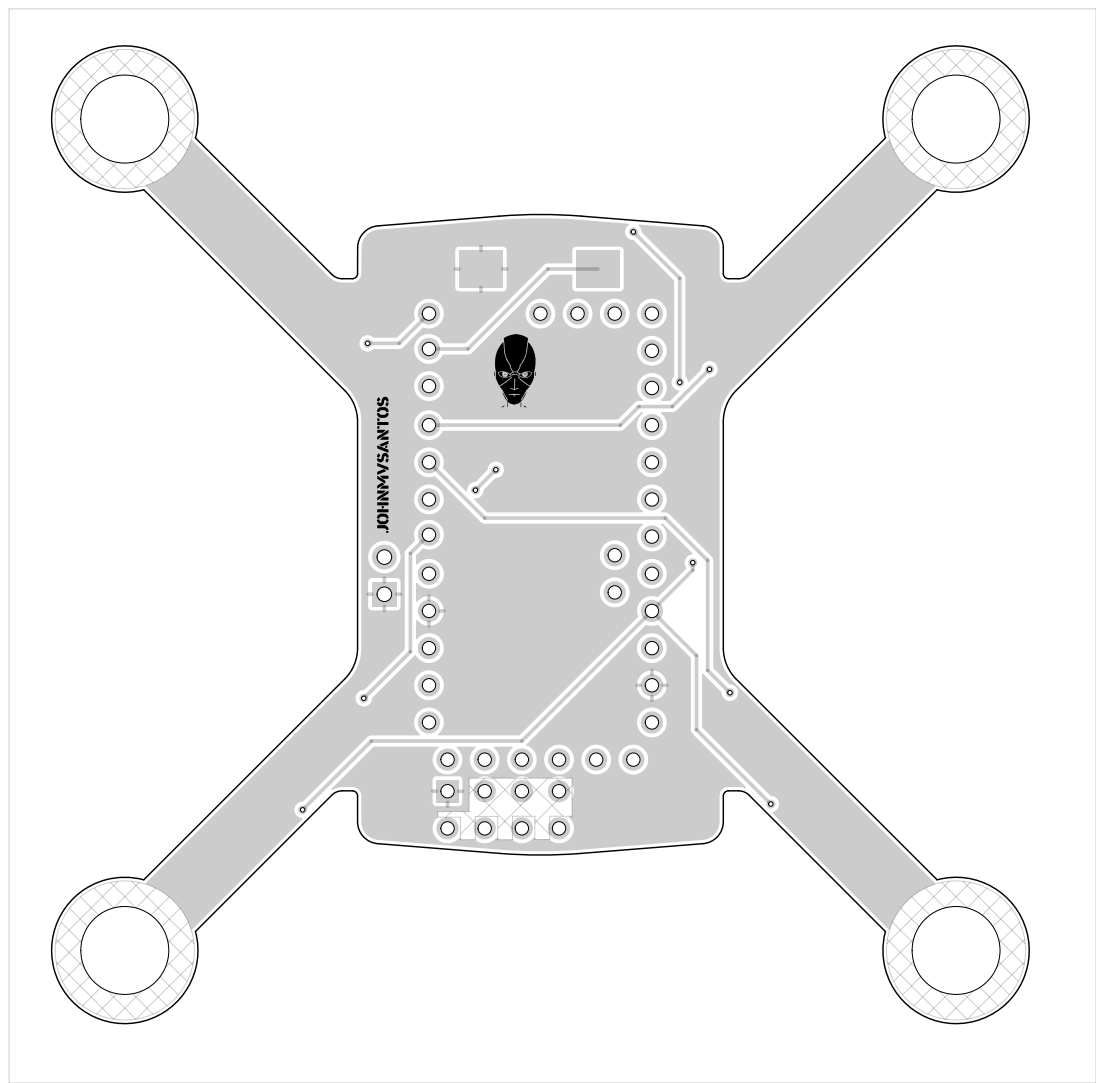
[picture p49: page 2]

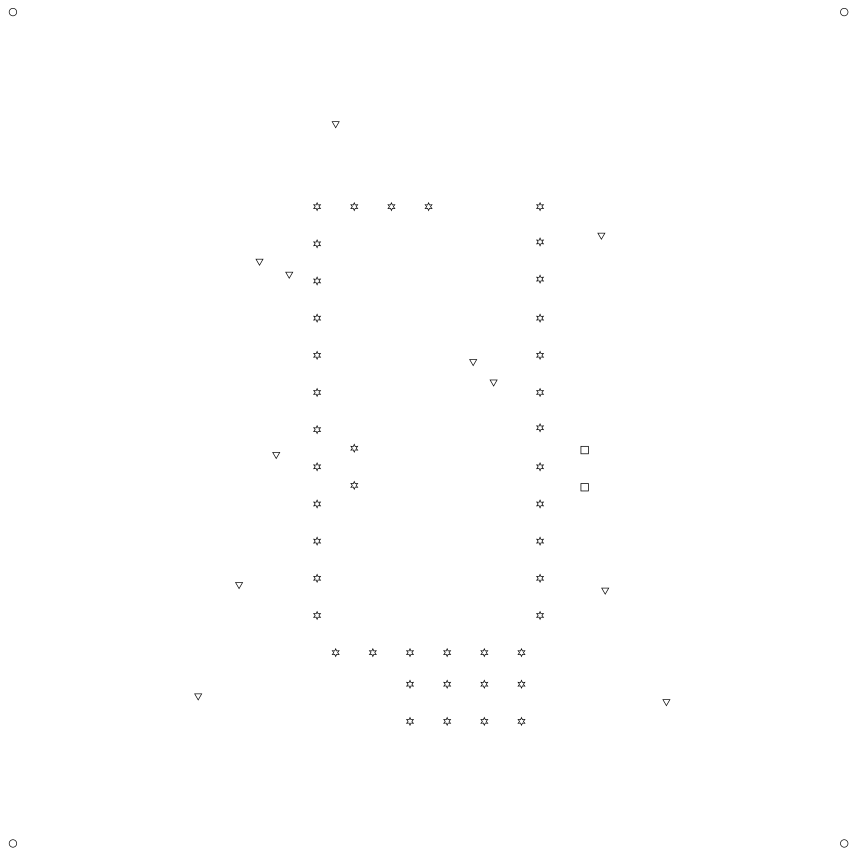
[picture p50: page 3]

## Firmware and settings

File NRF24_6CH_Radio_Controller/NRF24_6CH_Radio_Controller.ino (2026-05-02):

/*A basic 6 channel transmitter using the nRF24L01 module.*/
/* Like, share and subscribe, ELECTRONOOBS */
/* http://www.youtube/c/electronoobs */

/* First we include the libraries. Download it from
   my webpage if you donw have the NRF24 library */

#include <SPI.h>
#include <nRF24L01.h>             //Downlaod it here: https://www.electronoobs.com/eng_arduino_NRF24_lib.php
#include <RF24.h>

/*Create a unique pipe out. The receiver has to
  wear the same unique code*/

const uint64_t pipeOut = 0xE8E8F0F0E1LL; //IMPORTANT: The same as in the receiver!!!

RF24 radio(10, 9); // select  CE and CSN  pins

// The sizeof this struct should not exceed 32 bytes
// This gives us up to 32 8 bits channels
struct MyData {
  byte throttle;
  byte yaw;
  byte pitch;
  byte roll;
  byte AUX1;
  byte AUX2;
};

MyData data;

void resetData()
{
  //This are the start values of each channal
  //Throttle is 0 in order to stop the motors
  //127 is the middle value of the 10ADC.

  data.throttle = 0;
  data.yaw = 127;
  data.pitch = 127;
  data.roll = 127;
  data.AUX1 = 0;
  data.AUX2 = 0;
}

void setup()
{
  //Start everything up
  radio.begin();
  radio.setAutoAck(false);
  radio.setDataRate(RF24_250KBPS);
  radio.openWritingPipe(pipeOut);
  resetData();
  Serial.begin(9600);               // starting the Serial Monitor

  pinMode(5, INPUT_PULLUP);
  pinMode(3, INPUT_PULLUP);
}

/**************************************************/

// Returns a corrected value for a joystick position that takes into account
// the values of the outer extents and the middle of the joystick range.
int mapJoystickValues(int val, int lower, int middle, int upper, bool reverse)
{
  val = constrain(val, lower, upper);
  if ( val < middle )
    val = map(val, lower, middle, 0, 128);
  else
    val = map(val, middle, upper, 128, 255);
  return ( reverse ? 255 - val : val );
}

void loop()
{
  // The calibration numbers used here should be measured
  // for your joysticks till they send the correct values.
  data.throttle = mapJoystickValues( analogRead(A3), 0, 510, 1023, true );
  data.yaw      = mapJoystickValues( analogRead(A1), 0, 531, 1023, true );
  data.pitch    = mapJoystickValues( analogRead(A2), 0, 503, 1023, true );
  data.roll     = mapJoystickValues( analogRead(A6), 0, 512, 1023, true );

  // Serial.print("A6:");
  // Serial.print(analogRead(A6));

  // Serial.print(" A2:");
  // Serial.print(analogRead(A2));

  // Serial.print(" A1:");
  // Serial.print(analogRead(A1));

  // Serial.print(" A3:");
  // Serial.println(analogRead(A3));
  
  data.AUX1     = digitalRead(5);
  data.AUX2     = digitalRead(3);

  radio.write(&data, sizeof(MyData));
}

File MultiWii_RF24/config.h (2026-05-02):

#ifndef CONFIG_H_
#define CONFIG_H_

/*************************************************************************************************/
/****           CONFIGURABLE PARAMETERS                                                       ****/
/*************************************************************************************************/

/* this file consists of several sections
 * to create a working combination you must at least make your choices in section 1.
 * 1 - BASIC SETUP - you must select an option in every block.
 *      this assumes you have 4 channels connected to your board with standard ESCs and servos.
 * 2 - COPTER TYPE SPECIFIC OPTIONS - you likely want to check for options for your copter type
 * 3 - RC SYSTEM SETUP
 * 4 - ALTERNATE CPUs & BOARDS - if you have
 * 5 - ALTERNATE SETUP - select alternate RX (SBUS, PPM, etc.), alternate ESC-range, etc. here
 * 6 - OPTIONAL FEATURES - enable nice to have features here (FlightModes, LCD, telemetry, battery monitor etc.)
 * 7 - TUNING & DEVELOPER - if you know what you are doing; you have been warned
 *     - (ESCs calibration, Dynamic Motor/Prop Balancing, Diagnostics,Memory savings.....)
 * 8 - DEPRECATED - these features will be removed in some future release
 */

/* Notes:
 * 1. parameters marked with (*) in the comment are stored in eeprom and can be changed via serial monitor or LCD.
 * 2. parameters marked with (**) in the comment are stored in eeprom and can be changed via the GUI
 */


/*************************************************************************************************/
/*****************                                                                 ***************/
/****************  SECTION  1 - BASIC SETUP                                                *******/
/*****************                                                                 ***************/
/*************************************************************************************************/

  /**************************    The type of multicopter    ****************************/
    //#define GIMBAL
    //#define BI
    //#define TRI
    //#define QUADP
    #define QUADX
    //#define Y4
    //#define Y6
    //#define HEX6
    //#define HEX6X
    //#define HEX6H  // New Model
    //#define OCTOX8
    //#define OCTOFLATP
    //#define OCTOFLATX
    //#define FLYING_WING
    //#define VTAIL4
    //#define AIRPLANE
    //#define SINGLECOPTER
    //#define DUALCOPTER
    //#define HELI_120_CCPM
    //#define HELI_90_DEG

  /****************************    Motor minthrottle    *******************************/
    /* Set the minimum throttle command sent to the ESC (Electronic Speed Controller)
       This is the minimum value that allow motors to run at a idle speed  */
    //#define MINTHROTTLE 1300 // for Turnigy Plush ESCs 10A
    //#define MINTHROTTLE 1120 // for Super Simple ESCs 10A
    //#define MINTHROTTLE 1064 // special ESC (simonk)
    #define MINTHROTTLE 1050 // for brushed ESCs like ladybird
    //#define MINTHROTTLE 1000 // (*) (**)

  /****************************    Motor maxthrottle    *******************************/
    /* this is the maximum value for the ESCs at full power, this value can be increased up to 2000 */
    #define MAXTHROTTLE 2000

  /****************************    Mincommand          *******************************/
    /* this is the value for the ESCs when they are not armed
       in some cases, this value must be lowered down to 900 for some specific ESCs, otherwise they failed to initiate */
    #define MINCOMMAND  1000

  /**********************************  I2C speed for old WMP config (useless config for other sensors)  *************/
    #define I2C_SPEED 100000L     //100kHz normal mode, this value must be used for a genuine WMP
    //#define I2C_SPEED 400000L   //400kHz fast mode, it works only with some WMP clones

  /***************************    Internal i2c Pullups   ********************************/
    /* enable internal I2C pull ups (in most cases it is better to use external pullups) */
    //#define INTERNAL_I2C_PULLUPS

  /**********************************  constant loop time  ******************************/
    #define LOOP_TIME 2800

  /**************************************************************************************/
  /*****************          boards and sensor definitions            ******************/
  /**************************************************************************************/
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

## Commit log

2025-06-01 Added Arduino software for the drone transmitter and reciever. Also added credits to the design components in the ReadMe. Added todo.txt to the repo.
    [config.h]
2025-06-08 Adding prototypes documentation
2025-06-08 Added ReadMe prototype 1 description and also sphinx documentation. Added electrical schematic and diagrams and images.
2025-06-09 Added documentation for the drone materials and the prototype 1 issues. Added PDF documentation.
2025-06-10 Adding initial reflection to prototype one. WIP
2025-07-23 Prototype 1.1 Documentation and Reflection.
2025-08-19 Added reflection and documentation of prototype v1.3.
2025-08-31 Prototype Version 1.3. Updated the schematics and the NRF24L01 controller code to remove the LCD. Added reflection and details for this prototype. Doc updates and link to the youtube video that demos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
2025-09-02 Reviewed current documentation and fixes to correct grammar or formatting issues.
2025-12-01 Added prototype v1.4 reflection and update.
2026-03-27 Added prototype 2.0 design files (WIP). Added EasyEDA schematics and PCB, and Fusion360 DXF files. Also new screenshots. Updated ReadMe changelog and added key takeaways/learnings. Updated prototypes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
    [controller_sketch.dxf, drone_sketch.dxf]
2026-03-28 Add design_files directory to contain all design components. Add gerber files for the drone and the controller. Add DXF files from Fusion360 for the template PCB. Update controller and drone instruct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
    [controller_sketch.dxf, drone_sketch.dxf]
2026-03-29 Added prototype 2.0 screenshots. Updated drone instructions with the latest prototype.
2026-03-29 Added prototype 2.0 screenshot
2026-03-29 Add ReadMe video link to prototype 2.0
2026-04-27 Added prototype v2.1 reflection and description. Also updated ReadMe Changelog with this prototype.
2026-04-28 Updated screenshots and build with prototype v2.1. Also updated PDF documentation with prototype v2.1
2026-04-28 Added Zip gerber files under design_files and also removed the Identifier file
2026-04-28 Added Zip Gerber files under design_files
2026-05-02 * Updated Gerber files with v2.1 releases * Updated docs and instructions to match v2.1 * Updated software controller to match v2.1 * Updated software drone output.cpp for correct motor mapping, nrf2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
    [config.h]
2026-06-30 Added README section for PCBWay experience.
2026-06-30 Add assets from PCBWay review
2026-06-30 Update README to include project link and image
    Restored EasyEDA project link and prototype image to README.
